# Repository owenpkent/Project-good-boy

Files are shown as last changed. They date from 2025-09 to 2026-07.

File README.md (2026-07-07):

# Project Good Boy

An open-source battery powered dog treat dispenser that is activated via a web interface and is wheelchair mountable.
It is currently compatible with being mounted on 40x40 aluminum extrusions. 

**Want one built for you? Or modifications/additional support?** Reach out—we'd be happy to help!

If you are interested in us developing this as a product, please take the survey.

Survey: https://tinyurl.com/m8z8fjtb

---

## Contact

Owen Kent - https://okstud.io/

Marshall Saltz - https://saltztech.com/

---

## Features

- **Wi-Fi Control** — Operates on your local network or as its own access point
- **Web Interface** — Phone-friendly UI served directly from the device
- **Battery Powered** — Uses a 12 V Lipo to power the system
- **Accessible Design** — Large buttons, simple controls, wheelchair-mountable
---

## Bill of Materials

| Component | Amount | Link |
|---|---|---|
| Battery | 1 | [Amazon](https://www.amazon.com/dp/B0D9D8ZSV9) |
| Nema 17 Stepper Motor | 1 | [Amazon](https://www.amazon.com/dp/B07PNV7RBW) |
| TMC2209 Stepper Motor Driver | 1 | [Amazon](https://www.amazon.com/dp/B07ZPYKL46) |
| 12V to 5V DC Converter | 1 | [Amazon](https://www.amazon.com/dp/B08VHZJ3C8) |
| 8mm M3 Bolts | 4 | [Amazon](https://www.amazon.com/dp/B0C7ZRTH3Q) |
| Jumper Wires | —| — |
| Filament (preferably PETG) | — | — |
| T-nuts for mounting | 5 | — |
| T-nut compatible bolts | 5 | — |
| ESP32 Dev Kit | 1 | — |
| Wagu Wire Connectors | — | — |
| ArtResin or another safe resin | — | — |
| 100 uF Capacitor | 1 | - |

---

### Tools Required

- Pliers
- Electronics screwdriver
- USB-C cable (for uploading firmware and charging)
- 3D printer
- Flat edge screwdriver

---

## Wiring

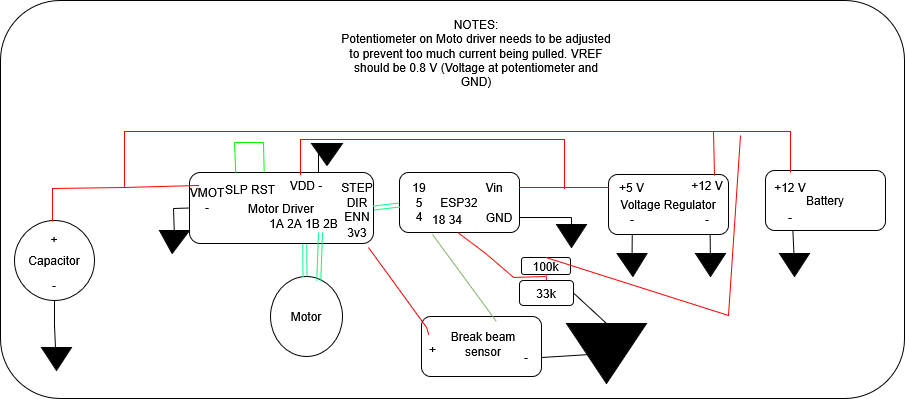
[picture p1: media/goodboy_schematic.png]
Schematic


---

## Building & Uploading

### Assembly Instructions

Assembly video or image series needed here!

### Prerequisites

Install [Arduino IDE](https://www.arduino.cc/en/software)
Required libraries:
   - `Wifi`
   - `ESPAsyncWebServer.h`
   - `AsyncTCP`
   - `DNSServer`
   - `ESPmDNS`
   - `LittleFS` [Random Nerd Tutorials](https://randomnerdtutorials.com/esp32-littlefs-arduino-ide/)

### Upload Firmware

1. Download module_ver/project_goodboy folder

2. Connect the ESP32 via USB-C and open project_goodboy.ino in Arduino IDE
   
3. Upload the data folder to the ESP32 using LittleFS (See [Random Nerd Tutorials](https://randomnerdtutorials.com/esp32-littlefs-arduino-ide/) for further instruction)

4. Upload sketch

## Usage

### First Boot (Access Point Mode)

1. Power on the device
2. Connect to Wi-Fi network: **GoodBoy** (password: `buddythedog`)
3. Open browser: `http://192.168.4.1` if pop-up does not open automatically
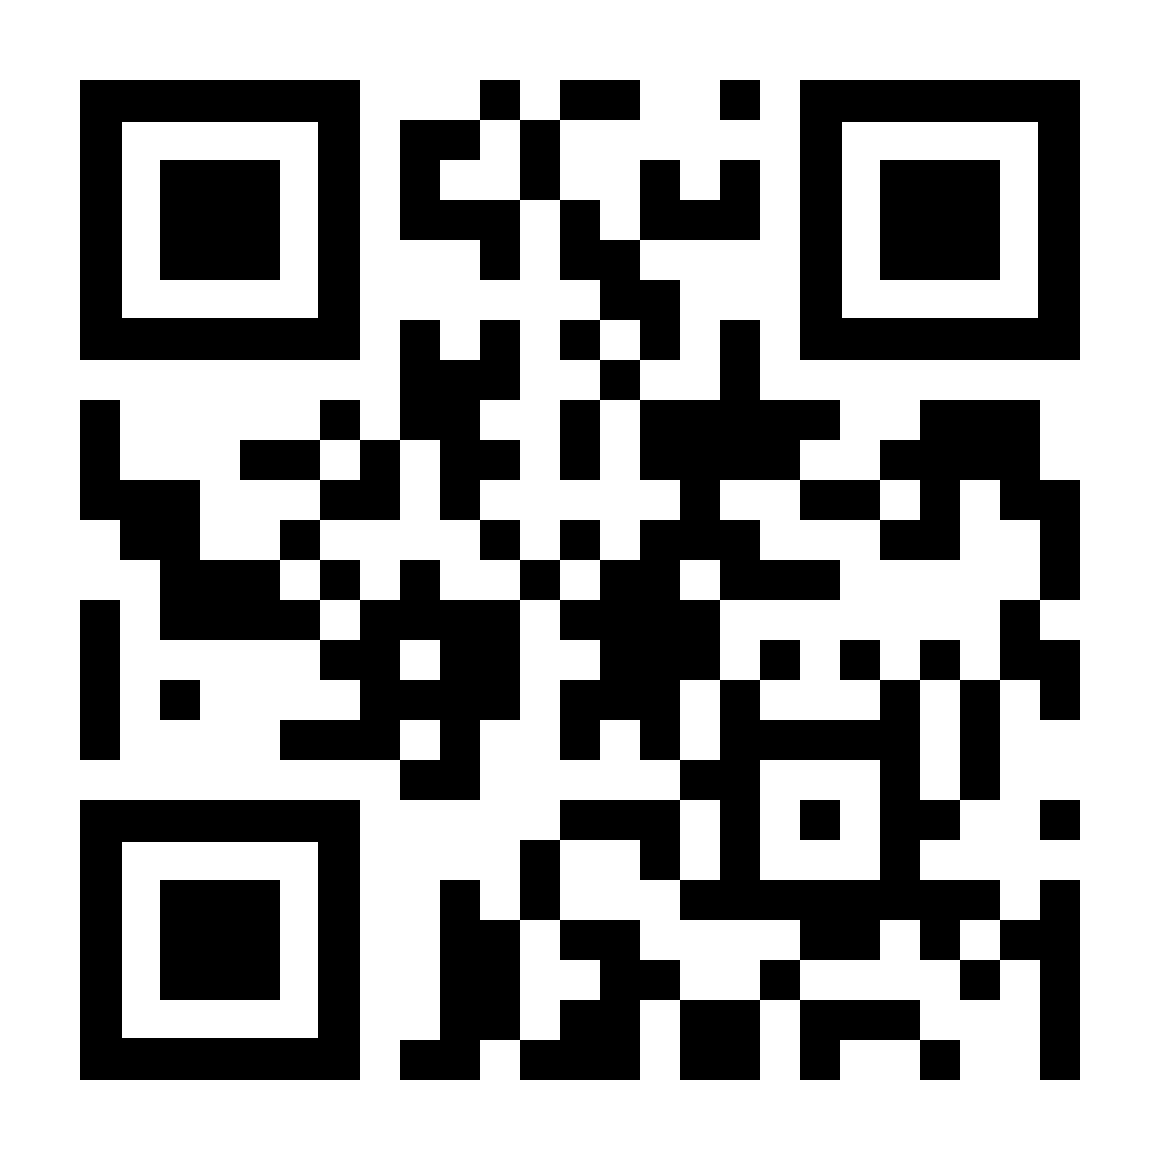
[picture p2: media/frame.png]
QR

4. Enter your home Wi-Fi credentials to connect the device to your network

### Normal Operation

1. Connect to the same Wifi network as the device
2. Open browser: `http://goodboy.local` (or check serial output for IP)
3. Use the web interface:
   - **Dispense** — Triggers the motor to dispense a treat
   - **Speed** — Adjusts motor speed

Can also be used in AP mode by following steps 1-3 of First Boot

---

### Maintainance
This dispenser must be cleaned regularly. To clean, wipe down with a damp paper towel or food-safe cleaner. The parts can be submerged for a deeper clean as long as all electronics are disconnected including the motor and sensors.

---

## TODO

- [ ] Include assembly instructions/video
- [ ] Video of operation
- [ ] Include sensor instructions, aperture models, etc.
---

## Contributing

Issues and PRs welcome! Please open an issue before proposing major changes.

---

## License

MIT License — see `LICENSE`.

---

## Credits

Built with love for a very good boy.

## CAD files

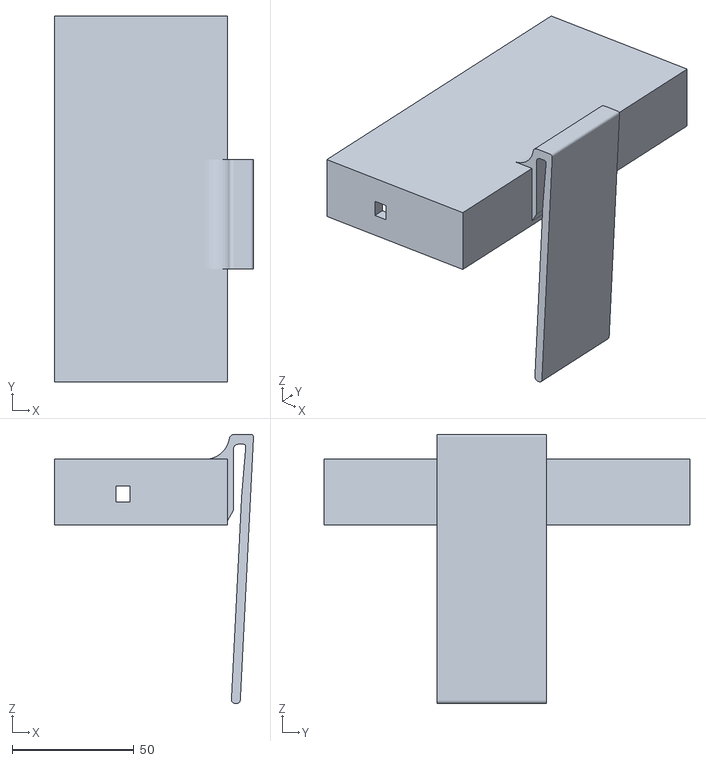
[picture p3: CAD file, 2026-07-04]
models/top.stl
81.6 x 150.0 x 110.3

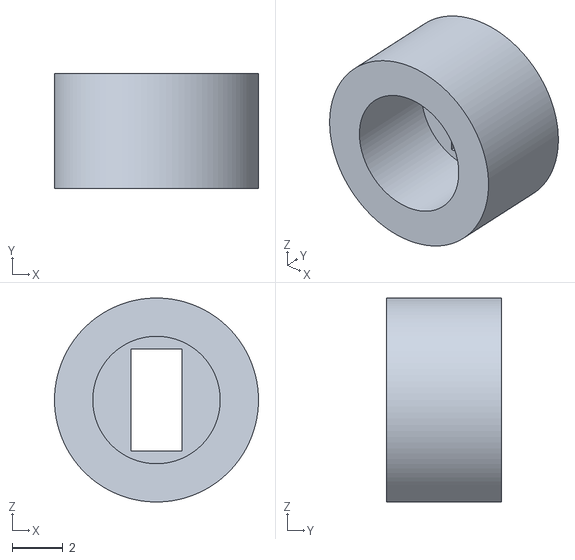
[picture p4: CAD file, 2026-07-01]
models/slot_apert.stl
8.00 x 4.50 x 8.00

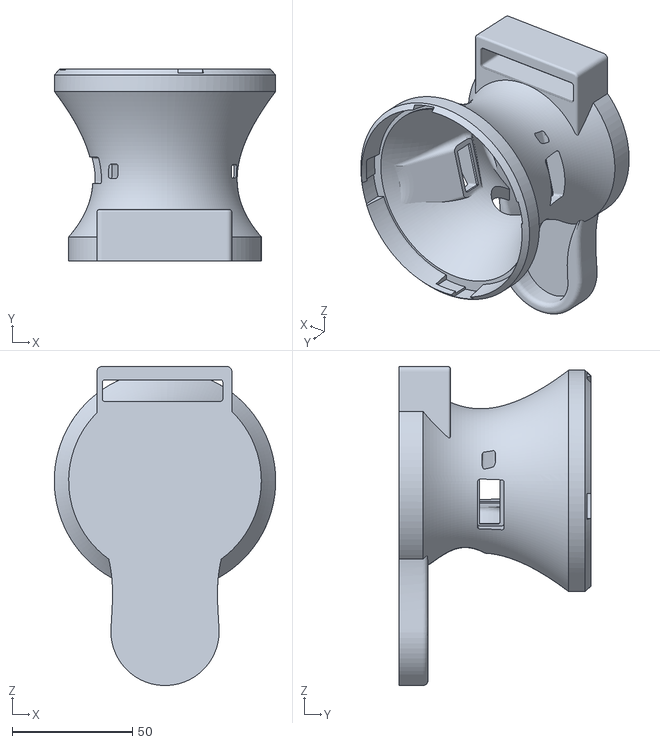
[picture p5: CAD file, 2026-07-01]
models/dispenser.stl
92.0 x 79.6 x 132.5

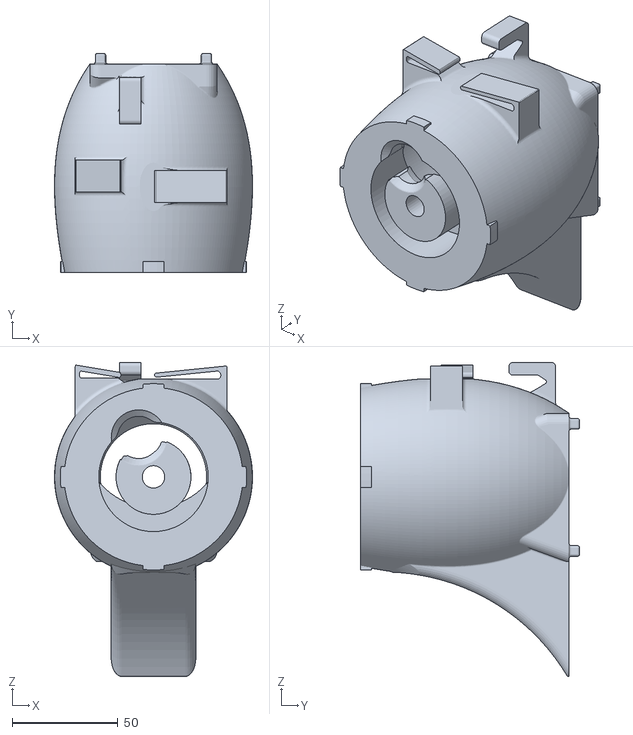
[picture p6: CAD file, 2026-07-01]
models/holder.stl
93.5 x 103.6 x 148.3

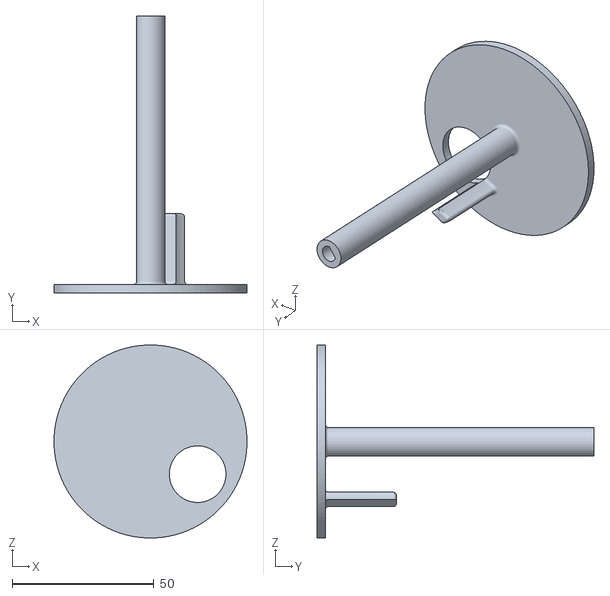
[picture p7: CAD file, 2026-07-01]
models/agitator.stl
68.2 x 97.7 x 68.2

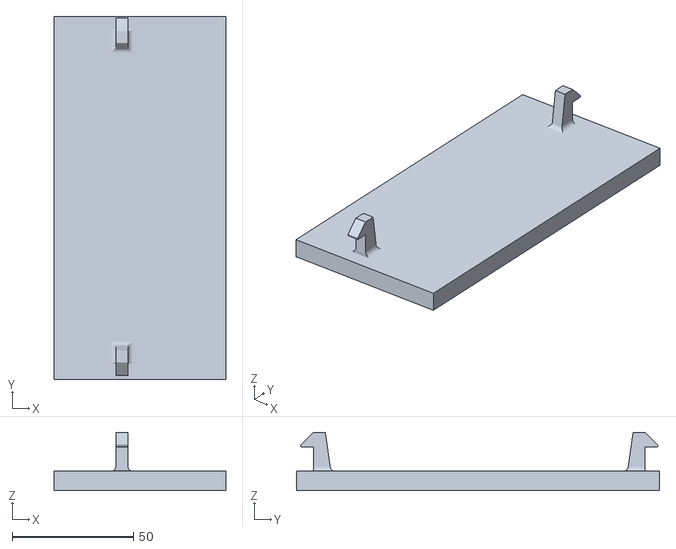
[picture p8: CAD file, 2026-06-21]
models/bottom.stl
71.0 x 150.0 x 24.0

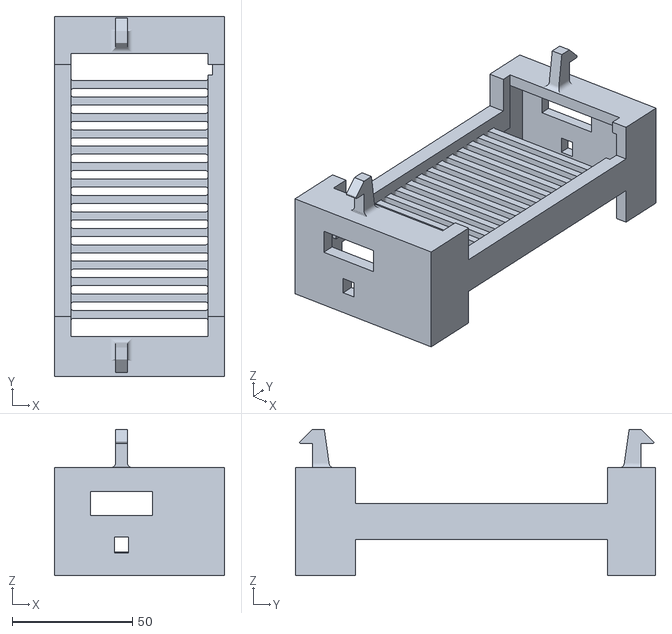
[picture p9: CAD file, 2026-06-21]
models/middle.stl
71.0 x 150.0 x 61.0

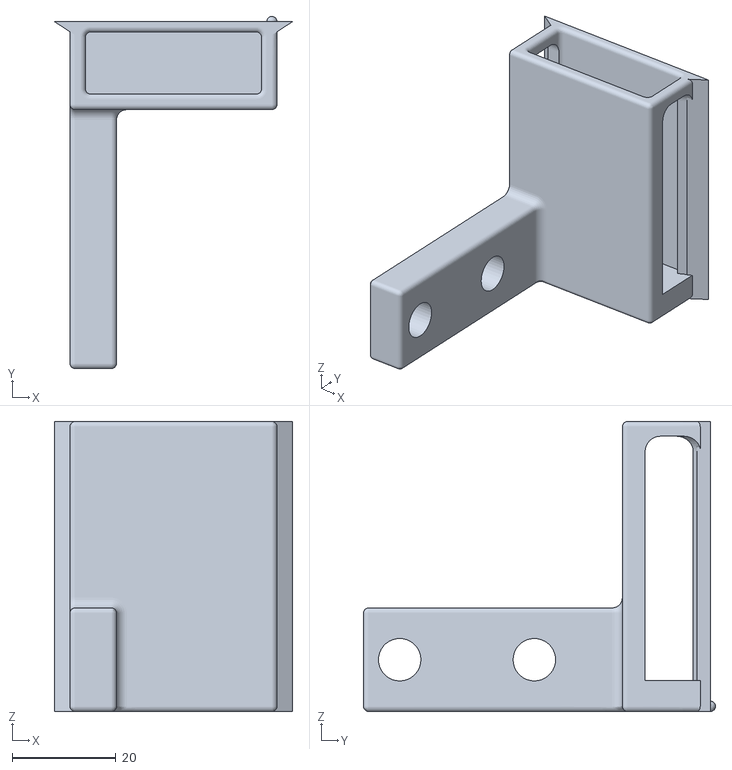
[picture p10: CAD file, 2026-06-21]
models/recorder_mount.stl
46.0 x 68.0 x 56.0

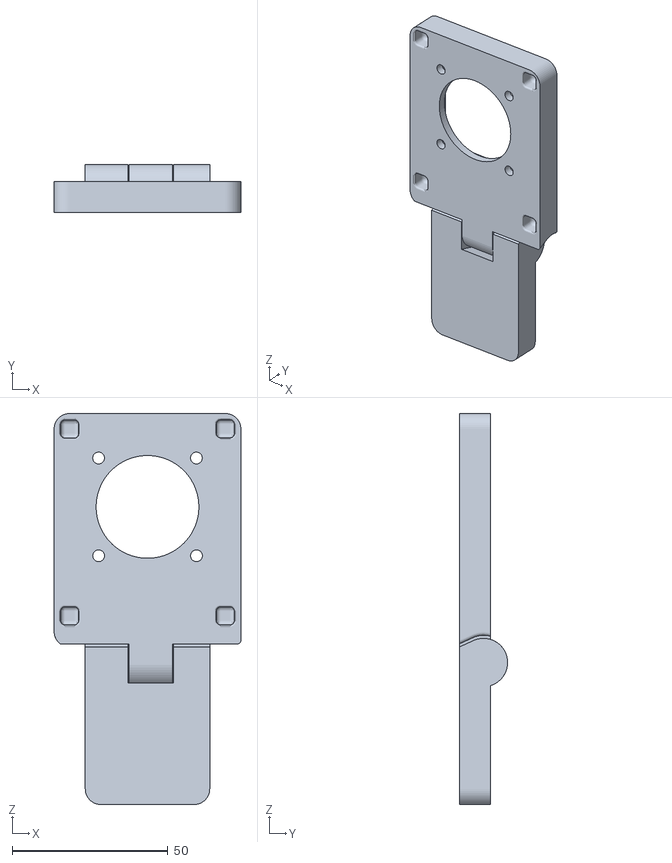
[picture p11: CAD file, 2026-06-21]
models/lid.stl
60.0 x 15.5 x 125.6

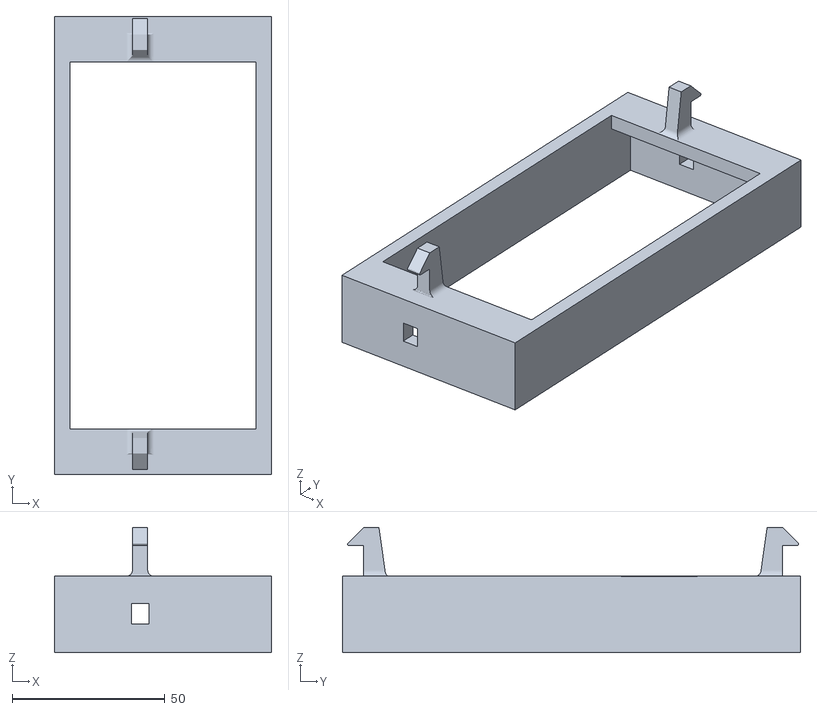
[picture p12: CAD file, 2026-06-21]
models/spacer.stl
71.0 x 150.0 x 41.0

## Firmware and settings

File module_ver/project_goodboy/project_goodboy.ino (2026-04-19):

/*
  Sources:

  FreeRTOS API and Examples - freertos.org

  Espressif Systems docs.espressif.com

  ChatGPT - OpenAI.com

  Rui Santos - RandomNerdTutorials.com

  Last Minute Engineers - https://lastminuteengineers.com/a4988-stepper-motor-driver-arduino-tutorial/

  Adafruit Learn - https://learn.adafruit.com/ir-breakbeam-sensors/arduino

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
  The above copyright notice and this permission notice shall be included in all
  copies or substantial portions of the Software.
*/

#include <WiFi.h>
#include <ESPAsyncWebServer.h>
#include <AsyncTCP.h>
#include "LittleFS.h"
#include <DNSServer.h>
#include <ESPmDNS.h>
#include <driver/adc.h>
#include <AccelStepper.h>

#define STEPS_PER_REV 200
#define MIN_SPEED 100
#define MAX_SPEED 1000
#define R1 100000.0f   // 100k
#define R2 33000.0f    // 33k
#define ADC_MAX 4095.0f
#define ADC_REF 3.3f  
#define ACC 800

const char *AP_SSID = "GoodBoy";
const char *AP_PASS = "buddythedog";

const char *PARAM_INPUT_1 = "ssid";
const char *PARAM_INPUT_2 = "pass";

const char *ssidPath = "/ssid.txt";
const char *passPath = "/pass.txt";

DNSServer dnsServer;
AsyncWebServer server(80);

const int dir = 5;
const int stepp = 19;
const int breakBeam = 18;
const int enablePin = 4;
const int batt = 34;
volatile float g_battVoltage = 0.0f;
volatile bool stopRequested = false;
volatile bool isRunning = false;
String ssid, pass;

int breakState;

AccelStepper stepper(AccelStepper::DRIVER, stepp, dir);

TaskHandle_t TaskWiFiHandle = NULL;
QueueHandle_t stepperQueue = NULL;

typedef struct {
  int speed;
} StepperJob;

bool connectWiFi();
void startAP();
void startWebServer();
void initLittleFS();
void setupADC();
void saveCredentials(fs::FS &fs, const char *path, const char *message);
String loadCredentials(fs::FS &fs, const char *path);

/***********
* StepperTask - Free RTOS Task
* Handles stepper motor controls
* Recieves speed and on/off data via a queue/struct
* Recieves input from a break beam sensor to detect treat
*************/
void StepperTask(void *parameter) {
  StepperJob job;
  for (;;) {
    if (xQueueReceive(stepperQueue, &job, portMAX_DELAY) == pdTRUE) {
      stopRequested = false;
      isRunning = true;
      int spd = constrain(job.speed, MIN_SPEED, MAX_SPEED);
      digitalWrite(enablePin, LOW);
      stepper.setMaxSpeed(spd);
      stepper.setCurrentPosition(0);
      for (int j = 0; j < 3; ++j) {
        if (stopRequested) break;
        breakState = digitalRead(breakBeam);
        if (breakState == LOW) break;
        stepper.moveTo(200);
        while (stepper.distanceToGo() != 0) {
          stepper.run();
          if (stopRequested) {
            stepper.stop();
            while (stepper.isRunning()) {
              stepper.run(); 
            }
            break;
          }
          breakState = digitalRead(breakBeam);
          if (breakState == LOW){
            stepper.stop();
            break;
          }
        }
        stepper.setCurrentPosition(0);
        stepper.moveTo(-200);
        while (stepper.distanceToGo() != 0) {
          stepper.run();
          breakState = digitalRead(breakBeam);
          if (stopRequested) {
            stepper.stop();
            while (stepper.isRunning()) {
              stepper.run(); 
            }
            break;
          }
          breakState = digitalRead(breakBeam);
          if (breakState == LOW){
            stepper.stop();
            break;
          }
        }
      }
      isRunning = false;
      Serial.println("Stepper run complete.");
      digitalWrite(enablePin, HIGH);
    }
  }
}

/******
* RebootTask - Free RTOS Task
* Handles restarting ESP32 when needed
*******/
void RebootTask(void *param) {
  uint32_t ms = (uint32_t)(uintptr_t)param;
  vTaskDelay(ms / portTICK_PERIOD_MS);
  Serial.println("Restarting now...");
  ESP.restart();
  vTaskDelete(NULL);
}

/******
* BatteryTask - Free RTOS Task
* Reads battery voltage using a voltage divider
*******/
void BatteryTask(void *parameter) {
  for (;;) {
    int adc_raw = analogRead(34);
    float v_adc = (adc_raw / ADC_MAX) * ADC_REF;
    float v_batt = v_adc * ((R1 + R2) / R2);  // Compensate voltage divider
    g_battVoltage = v_batt;
    vTaskDelay(pdMS_TO_TICKS(1000));
  }
}

/****************
* WifiTask - FreeRTOS task
* Attempts to connect to a network.
* If that fails, sets up an access point.
* Opens connection to controls webpage.
*****************/
void WiFiTask(void *parameter) {
  Serial.println("WiFi Task started");
  
  ssid = loadCredentials(LittleFS, ssidPath);
  pass = loadCredentials(LittleFS, passPath);
  
  Serial.print("Loaded SSID: ");
  Serial.println(ssid.isEmpty() ? "(empty)" : ssid);
  
  if (connectWiFi()) {
    Serial.println("Connected to WiFi");
    if (MDNS.begin("goodboy")) {
     Serial.println("mDNS started: http://goodboy.local");
    } 
    else {
      Serial.println("mDNS failed");
    }
    } 
  else {
    Serial.println("Starting AP mode");
    startAP();
  }

  Serial.println("Starting web server");
  startWebServer();
  Serial.println("Web server started");
  
  vTaskSuspend(NULL);  
}

void setup() {
  Serial.begin(115200);
  delay(1000);
  pinMode(enablePin, OUTPUT);
  digitalWrite(enablePin, HIGH);
  pinMode(stepp, OUTPUT);
  pinMode(dir, OUTPUT);
  pinMode(breakBeam, INPUT_PULLUP);
  //Serial.print("Reset reason: ");
  //Serial.println(esp_reset_reason());
  initLittleFS();
  stepper.setAcceleration(ACC);
  stepperQueue = xQueueCreate(1, sizeof(StepperJob));

  if (stepperQueue == NULL) {
    Serial.println("Failed to create stepperQueue!");
  }

  xTaskCreatePinnedToCore(
    StepperTask,
    "StepperTask",
    4096,
    NULL,
    2,
    NULL,
    1);

  xTaskCreatePinnedToCore(
    WiFiTask,
    "WiFiTask",
    4096,
    NULL,
    1,
    &TaskWiFiHandle,
    0);

  xTaskCreatePinnedToCore(
    BatteryTask,
    "BatteryTask",
    2048,
    NULL,
    1,
    NULL,
    1
  );
}

/***********
* connectWifi - bool func
* Connects to saved credentials.
* Returns:
* false - starts AP (should open DNS automatically)
* true - connection successful, visit at http://goodboy.local
************/
bool connectWiFi() {
  WiFi.disconnect(true);
  if (ssid.isEmpty() || pass.isEmpty()) {
    return false;
  }
  
  WiFi.mode(WIFI_STA);
  WiFi.begin(ssid.c_str(), pass.c_str());

  unsigned long start = millis();
  
  while (WiFi.status() != WL_CONNECTED && millis() - start < 10000) {
    vTaskDelay(pdMS_TO_TICKS(500));
  }

  if (WiFi.status() == WL_CONNECTED) {
    Serial.print("Device IP: ");
    Serial.println(WiFi.localIP().toString());
    return true;
  }
  return false;
}

/**********
* startAP - void funct
* Starts access point at: http://192.168.4.1
***********/
void startAP() {
  Serial.println("Setting WiFi mode to AP");
  WiFi.mode(WIFI_AP);
  IPAddress apIP(192, 168, 4, 1);
  IPAddress gateway(192, 168, 4, 1);
  IPAddress subnet(255, 255, 255, 0);
  Serial.println("Configuring AP");
  WiFi.softAPConfig(apIP, gateway, subnet);
  Serial.print("Starting AP: ");
  Serial.println(AP_SSID);
  WiFi.softAP(AP_SSID, AP_PASS);
  Serial.println("Starting DNS server");
  dnsServer.start(53, "*", WiFi.softAPIP()); 
  Serial.print("AP IP: ");
  Serial.println(WiFi.softAPIP());
  Serial.println("AP setup complete");
}

/*******
* startWebServer - void funct
* Starts webpage, controls:
* stepper (dog treat dispenser)
* saving wifi credentials
********/
void startWebServer() {
  server.onNotFound([](AsyncWebServerRequest *request){
    request->send(200, "text/plain", "Not found");
  });

  server.on("/", HTTP_GET, [](AsyncWebServerRequest *request) {
    request->send(LittleFS, "/index.html", "text/html");
  });

  server.serveStatic("/", LittleFS, "/");
  
  server.on("/hotspot-detect.html", HTTP_GET, [](AsyncWebServerRequest *request){
    request->redirect("/");
  });

  server.on("/connecttest.txt", HTTP_GET, [](AsyncWebServerRequest *request){
    request->redirect("/");
  });

  server.on("/ncsi.txt", HTTP_GET, [](AsyncWebServerRequest *request){
    request->redirect("/");
  });

  server.on("/stop", HTTP_GET, [](AsyncWebServerRequest *request) {
    if (isRunning){
     stopRequested = true;
    }
    request->send(200, "text/plain", "Stop Sent");
  });

  server.on("/voltage", HTTP_GET, [](AsyncWebServerRequest *request){
    char buf[16];
    snprintf(buf, sizeof(buf), "%.2f", g_battVoltage);
    request->send(200, "application/json", String("{\"voltage\":") + buf + "}");
  });

  server.on("/run", HTTP_GET, [](AsyncWebServerRequest *request) {
    stopRequested = false;
    int spd = MIN_SPEED;
    if (request->hasParam("speed")) {
      spd = constrain(request->getParam("speed")->value().toInt(), MIN_SPEED, MAX_SPEED);
    }
    StepperJob job;
    job.speed = spd;
    xQueueOverwrite(stepperQueue, &job);
    Serial.println("Job sent to queue");
    request->send(200, "text/plain", "Stepper command updated");
  });

  server.on("/", HTTP_POST, [](AsyncWebServerRequest *request) {
    int params = request->params();
    for (int i = 0; i < params; i++) {
      const AsyncWebParameter *p = request->getParam(i);
      if (p->isPost()) {
        if (p->name() == PARAM_INPUT_1) {
          ssid = p->value();
          saveCredentials(LittleFS, ssidPath, ssid.c_str());
        }
        if (p->name() == PARAM_INPUT_2) {
          pass = p->value();
          saveCredentials(LittleFS, passPath, pass.c_str());
        }
      }
    }
    request->send(200, "text/plain", "Credentials saved, restarting in 5s");
    const uint32_t delayMs = 5000;
    xTaskCreatePinnedToCore(
      RebootTask,
      "rebooter",
      2048,
      (void*)(uintptr_t)delayMs,
      1,
      NULL,
      1);
  });
  
  server.on("/generate_204", HTTP_GET, [](AsyncWebServerRequest *request){
    request->redirect("/");
  });

  server.begin();
}

/*****
* initLittleFS - void funct
******/
void initLittleFS() {
  if (!LittleFS.begin(true)) {
    Serial.println("LittleFS mount failed!");
  } 
  else {
    Serial.println("LittleFS mounted.");
  }
}

/****
* saveCredentials - void funct
* Parameters: file, path to save credentials to, credentials to save
* Saves wifi credentials to txt file in littleFS
*****/
void saveCredentials(fs::FS &fs, const char *path, const char *message) {
  File file = fs.open(path, FILE_WRITE);
  if (!file) {
    Serial.printf("Failed to open %s for writing\n", path);
    return;
  }
  file.print(message);
  file.close();
  Serial.printf("Saved %s\n", path);
}

/*****
* loadCredentials - String funct
* Parameters: file system, path to nab credentials from
* loads credentials from txt in littleFS
******/
String loadCredentials(fs::FS &fs, const char *path) {
  File file = fs.open(path);
  if (!file || file.isDirectory()) {
    return "";
  }
  String content = file.readStringUntil('\n');
  file.close();
  return content;
}

void setupADC() {
    analogReadResolution(12);           
    analogSetAttenuation(ADC_11db);    
}

void loop() {
 if (WiFi.getMode() == WIFI_AP) {
    dnsServer.processNextRequest();
  }
  vTaskDelay(pdMS_TO_TICKS(10));
}

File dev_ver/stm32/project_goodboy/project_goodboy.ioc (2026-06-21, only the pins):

Mcu.UserName=STM32G071CBTx
PA10.Signal=USART1_RX
PA13.Signal=SYS_SWDIO
PA14-BOOT0.Signal=SYS_SWCLK
PA4.Signal=GPIO_Output
PA6.Signal=GPIO_Output
PA7.Signal=GPIO_Output
PA9.Signal=USART1_TX
PB0.Signal=GPXTI0
PB7.Signal=I2C1_SDA
PB8.Signal=I2C1_SCL

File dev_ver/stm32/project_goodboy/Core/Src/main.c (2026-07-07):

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
/* Includes ------------------------------------------------------------------*/
#include "main.h"
/* USER CODE BEGIN PD */
#define CMD_STOP       0
#define CMD_DISPENSE   1

#define ENN_PIN        GPIO_PIN_4
#define ENN_PORT       GPIOA

#define STEP_PIN       GPIO_PIN_6
#define STEP_PORT      GPIOA

#define DIR_PIN        GPIO_PIN_7
#define DIR_PORT       GPIOA

#define BREAKBEAM_PIN  GPIO_PIN_0
#define BREAKBEAM_PORT GPIOB
/* USER CODE END PD */

I2C_HandleTypeDef hi2c1;

TIM_HandleTypeDef htim3;

UART_HandleTypeDef huart1;

/* USER CODE BEGIN PV */
typedef struct __attribute__((packed))
{
    uint8_t command;
    uint16_t speed;
} StepperCommand;

volatile StepperCommand rxCmd;

volatile uint8_t dispenseRequested = 0;
volatile uint8_t stopRequested = 0;
volatile uint8_t treatDetected = 0;

volatile uint32_t stepsRemaining = 0;
volatile uint8_t stepState = 0;
volatile uint8_t motorRunning = 0;
volatile uint16_t dispenseSpeed = 500;
/* USER CODE END PV */
/* USER CODE END PV */

void SystemClock_Config(void);
static void MX_GPIO_Init(void);
static void MX_USART1_UART_Init(void);
static void MX_TIM3_Init(void);
static void MX_I2C1_Init(void);
/* USER CODE BEGIN 0 */
void SetStepperSpeed(uint16_t speedHz)
{
    if(speedHz < 10)
        speedHz = 10;

    if(speedHz > 5000)
        speedHz = 5000;

    /*
     * TIM3 clock:
     * 64 MHz system clock
     * Prescaler = 63
     * Timer tick = 1 MHz
     */

    uint32_t timer_clk = HAL_RCC_GetPCLK1Freq() * 2UL;

    uint32_t period = (timer_clk / (speedHz * 2UL)) - 1UL;

    if (period > 65535) period = 65535;

    __HAL_TIM_SET_AUTORELOAD(&htim3, period);
    __HAL_TIM_SET_COUNTER(&htim3, 0);
}
void StartMove(uint32_t steps,
               GPIO_PinState dir)
{
	SetStepperSpeed(dispenseSpeed);

    HAL_GPIO_WritePin(DIR_PORT,
                      DIR_PIN,
                      dir);

    stepsRemaining = steps;

    motorRunning = 1;

    HAL_TIM_Base_Start_IT(&htim3);

    stepState = 0;

    HAL_GPIO_WritePin(STEP_PORT,
                      STEP_PIN,
                      GPIO_PIN_RESET);
}


void DispenseCycle(void)
{
    stopRequested = 0;
    treatDetected = 0;
    uint32_t MOVE_STEPS = 1600;

    HAL_GPIO_WritePin(ENN_PORT,
                      ENN_PIN,
                      GPIO_PIN_RESET);

    for(int i=0;i<1;i++)
    {
        StartMove(MOVE_STEPS, GPIO_PIN_SET);

        while(motorRunning)
        {
        }

        if(stopRequested || treatDetected)
            break;

        StartMove(MOVE_STEPS, GPIO_PIN_RESET);

        while(motorRunning)
        {
        }

        if(stopRequested || treatDetected)
            break;
    }

    HAL_GPIO_WritePin(ENN_PORT,
                      ENN_PIN,
                      GPIO_PIN_SET);
}
/* USER CODE END 0 */

/**
  * @brief  The application entry point.
  * @retval int
  */
int main(void)
{

  /* MCU Configuration--------------------------------------------------------*/

  /* Reset of all peripherals, Initializes the Flash interface and the Systick. */
  HAL_Init();

  /* Configure the system clock */
  SystemClock_Config();

  /* Initialize all configured peripherals */
  MX_GPIO_Init();
  MX_USART1_UART_Init();
  MX_TIM3_Init();
  MX_I2C1_Init();
  /* USER CODE BEGIN 2 */
  HAL_I2C_Slave_Receive_IT(
            &hi2c1,
            (uint8_t*)&rxCmd,
            sizeof(rxCmd));

    HAL_I2C_EnableListen_IT(&hi2c1);

    HAL_GPIO_WritePin(ENN_PORT,
                      ENN_PIN,
                      GPIO_PIN_SET);
  /* USER CODE END 2 */

  /* Infinite loop */
  /* USER CODE BEGIN WHILE */
  while(1){
      if (dispenseRequested && !motorRunning)
      {
          dispenseRequested = 0;
          DispenseCycle();
      }
  }
}
    /* USER CODE END WHILE */

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
/* USER CODE BEGIN 4 */
void HAL_GPIO_EXTI_Falling_Callback(uint16_t GPIO_Pin)
{
    if(GPIO_Pin == GPIO_PIN_0)
    {
        treatDetected = 1;
    }
}

void HAL_I2C_SlaveRxCpltCallback(I2C_HandleTypeDef *hi2c)
{
    switch(rxCmd.command)
    {
		case CMD_DISPENSE:

			dispenseSpeed = rxCmd.speed;

			if(dispenseSpeed < 100)
			    dispenseSpeed = 100;

			if(dispenseSpeed > 1000)
			    dispenseSpeed = 1000;

			SetStepperSpeed(dispenseSpeed);

			dispenseRequested = 1;

			break;

    	case CMD_STOP:
            stopRequested = 1;
            break;
    }

    HAL_I2C_Slave_Receive_IT(
        &hi2c1,
        (uint8_t*)&rxCmd,
        sizeof(rxCmd));
}

void HAL_I2C_ListenCpltCallback(I2C_HandleTypeDef *hi2c)
{
    HAL_I2C_EnableListen_IT(hi2c);
}
/* USER CODE END 4 */

/**
  * @brief  Period elapsed callback in non blocking mode
  * @note   This function is called  when TIM6 interrupt took place, inside
  * HAL_TIM_IRQHandler(). It makes a direct call to HAL_IncTick() to increment
  * a global variable "uwTick" used as application time base.
  * @param  htim : TIM handle
  * @retval None
  */
void HAL_TIM_PeriodElapsedCallback(TIM_HandleTypeDef *htim)
{
  /* USER CODE BEGIN Callback 0 */
	if(htim->Instance == TIM3)
	    {
	        if(!motorRunning)
	            return;

	        if(stopRequested || treatDetected)
	        {
	            motorRunning = 0;
	            HAL_TIM_Base_Stop_IT(&htim3);
	            return;
	        }

	        if(stepsRemaining == 0)
	        {
	            motorRunning = 0;
	            HAL_TIM_Base_Stop_IT(&htim3);
	            return;
	        }

	        if(stepState == 0)
	        {
	            HAL_GPIO_WritePin(STEP_PORT,
	                              STEP_PIN,
	                              GPIO_PIN_SET);

	            stepState = 1;
	        }
	        else
	        {
	            HAL_GPIO_WritePin(STEP_PORT,
	                              STEP_PIN,
	                              GPIO_PIN_RESET);

	            stepState = 0;

	            stepsRemaining--;
	        }
	    }

  /* USER CODE END Callback 0 */
  if (htim->Instance == TIM6)
  {
    HAL_IncTick();
  }
}

/**
  * @brief  This function is executed in case of error occurrence.
  * @retval None
  */
void Error_Handler(void)
{
}
#ifdef USE_FULL_ASSERT
/**
  * @brief  Reports the name of the source file and the source line number
  *         where the assert_param error has occurred.
  * @param  file: pointer to the source file name
  * @param  line: assert_param error line source number
  * @retval None
  */
void assert_failed(uint8_t *file, uint32_t line)
{
}
#endif /* USE_FULL_ASSERT */

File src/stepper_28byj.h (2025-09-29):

#pragma once
#include <Arduino.h>

// Simple 28BYJ-48 stepper driver for ULN2003 board (half-step sequence)
class Stepper28BYJ {
public:
  Stepper28BYJ(int in1, int in2, int in3, int in4, unsigned int stepDelayMicros = 1200)
  : p1(in1), p2(in2), p3(in3), p4(in4), delayUs(stepDelayMicros) {}

  void begin() {
    pinMode(p1, OUTPUT);
    pinMode(p2, OUTPUT);
    pinMode(p3, OUTPUT);
    pinMode(p4, OUTPUT);
    release();
  }

  // Set delay between half-steps (us). Larger = slower, more torque.
  void setDelayMicros(unsigned int us) { delayUs = us; }

  // Steps > 0 rotates forward; < 0 rotates backward
  void step(long steps) {
    if (steps == 0) return;
    const int dir = (steps > 0) ? 1 : -1;
    steps = labs(steps);
    while (steps--) {
      phase = (phase + dir) & 7; // wrap 0..7
      applyPhase(phase);
      delayMicroseconds(delayUs);
    }
    // Optional: hold torque by leaving coils energized; or call release() to save power
    release();
  }

  // Energize coils per half-step phase
  void applyPhase(uint8_t ph) {
    // Half-step 8-phase sequence
    static const uint8_t seq[8][4] = {
      {1,0,0,0},
      {1,1,0,0},
      {0,1,0,0},
      {0,1,1,0},
      {0,0,1,0},
      {0,0,1,1},
      {0,0,0,1},
      {1,0,0,1}
    };
    digitalWrite(p1, seq[ph][0]);
    digitalWrite(p2, seq[ph][1]);
    digitalWrite(p3, seq[ph][2]);
    digitalWrite(p4, seq[ph][3]);
  }

  // De-energize coils (reduce holding torque and save power)
  void release() {
    digitalWrite(p1, LOW);
    digitalWrite(p2, LOW);
    digitalWrite(p3, LOW);
    digitalWrite(p4, LOW);
  }

private:
  int p1, p2, p3, p4;
  unsigned int delayUs;
  int phase = 0;
};

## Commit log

2025-09-28 fix: portable Str alias, config conversions, ArduinoOTA include order; web mobile UI & simulator docs; native build cleanup
2025-09-29 feat(firmware): integrate 28BYJ-48 + ULN2003 stepper driver and /api/dispense endpoint
    Adds src/stepper_28byj.h, WebServer + DispenseTask in src/main.cpp, and status endpoint; updates README with wiring, firmware knobs, and TODO.
2025-10-05 Switch to Arduino CLI and g++; add tests; create GoodBoyStepper library; remove PlatformIO; clean .vscode; update README
2025-10-25 Add ESP32 stepper AP firmware and local UI preview: mock /run endpoint and preview-stepper.html
2025-12-21 Reorganize project: update README, add LICENSE and CONTRIBUTING, organize STL files into models/
    [BOM.xlsx, agitator_1.stl, bottom (2).stl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]
2025-12-21 Update README with correct BOM from CSV, reorganize firmware into proper Arduino folder structure, add schematic accuracy note
    [BOM.csv, BOM.xlsx]
2025-12-22 Updated readme, added renders, schematic
    [BOM.csv, agitator.stl, agitator_1.stl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]
2025-12-31 renaming, removed vacuum code
    [agitator.stl]
2026-03-12 now with break beam sensors!
2026-06-21 update readme, new design
    [agitator.stl, aluminum_bar_mount.stl, bottom.stl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]
